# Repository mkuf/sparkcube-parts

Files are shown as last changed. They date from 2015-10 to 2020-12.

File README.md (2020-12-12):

# sparkcube-parts
Modifications for the Sparklabs Sparkcube. <br>
<br>
All Parts can be printed without support. <br>
In Places where support is needed, there are small membranes that need to be drilled out after printing. <br>
See the "support" Folder in every FreeCAD File.

## case
Main File for anything related to the outer shell of the Printer. <br> 
These files are not compatible with the original Sparkcube, as my Printer is larger in X and Z. <br>
<br>
It sports a Electronics-Compartment made from bent Sheetmetal, Cutouts for fitting a Udoo Quad/Dual Board and a Touchscreen LCD Display. <br>
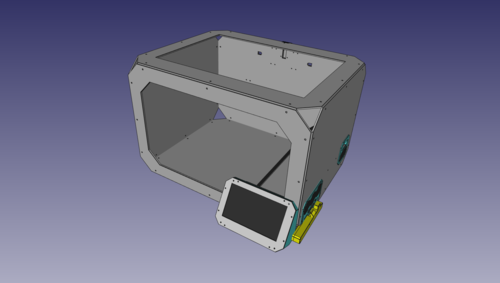
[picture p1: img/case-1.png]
case-1

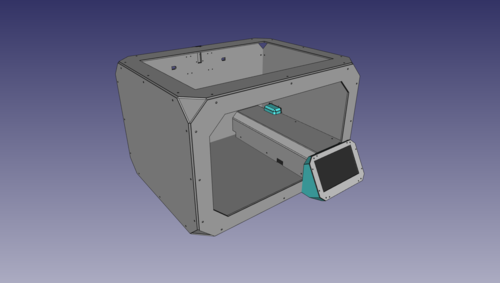
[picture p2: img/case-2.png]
case-2


## dual-mount
This is a X-Carriage and Mount for two E3Dv6 Hotends, as dropin for the stock Sparkcube carriage. <br>
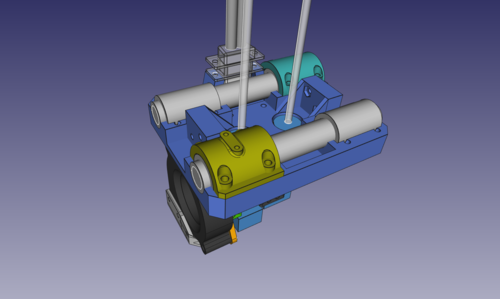
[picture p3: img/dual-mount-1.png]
dual-mount-1

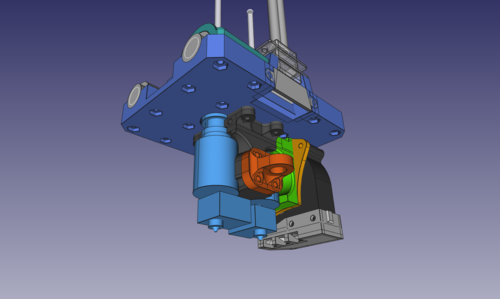
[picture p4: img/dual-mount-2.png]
dual-mount-2


## dual-x
With these Parts, a stock Sparkcube may be upgraded to use two independent Extruders for printing. <br>
Be aware that this reduces your Printarea in X by quite a bit. I recommend building your whole printer about 70mm wider. <br>
The design of these parts is inspired by the original Sparklab parts, but are not compatible with any of them (except the Z-Assembly of course). <br>
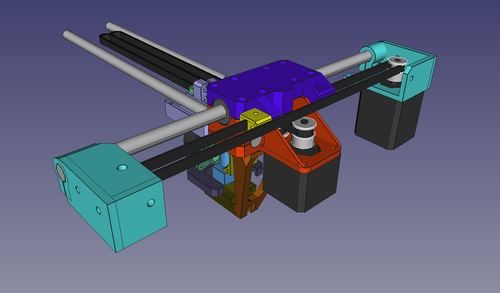
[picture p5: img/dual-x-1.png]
dual-x-1

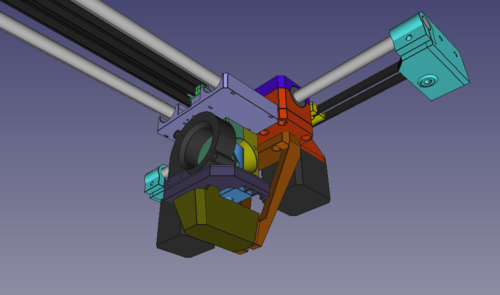
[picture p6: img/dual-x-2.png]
dual-x-2


## dual-x_z-assembly
Contains the `dual-x_bed_carrier`, that adjusts the placement of a standard MK2/3 Buildplate in Y to be compatible with the dual-x Setup <br>
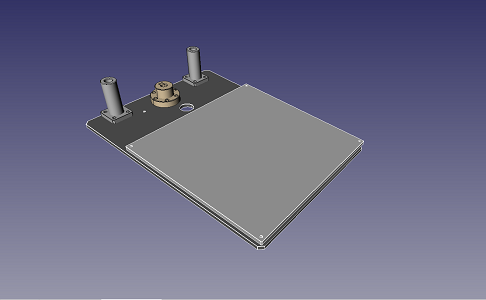
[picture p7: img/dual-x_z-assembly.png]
dual-x_z-assembly


## z-endstop-assembly
Minimalist solution to fine tune Z0. <br>
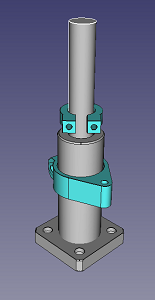
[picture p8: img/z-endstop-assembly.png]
z-endstop-assembly


## mpx-clip
A simple piece that clips around a MPX Connector to prevent it from accidential disconnecting. <br>
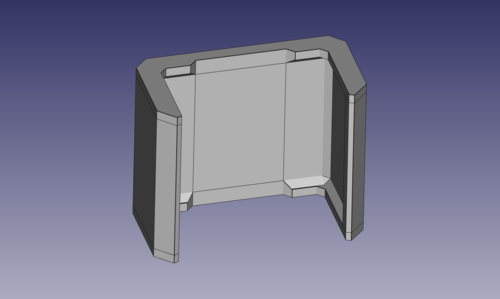
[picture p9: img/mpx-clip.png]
mpx-clip


## Spoolholder
A Spoolholder that is compatible with the Hole-Pattern found on the Back of the Case <br>
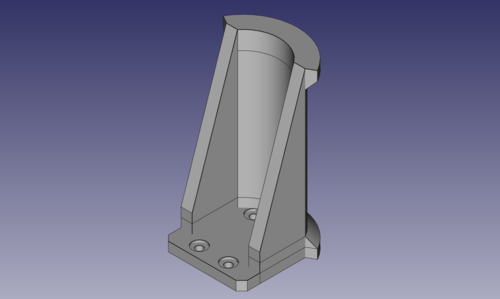
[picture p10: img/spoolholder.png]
spoolholder


## Webcam-Mount
A fixture to mount the PCB of a Logitech C270 Webcam to a Aluminium Extrusion without the need of any Screws. <br>
Just insert the Posts sideways into the Profile, rotate them 90°, screw in the baseplate and you're done. <br>
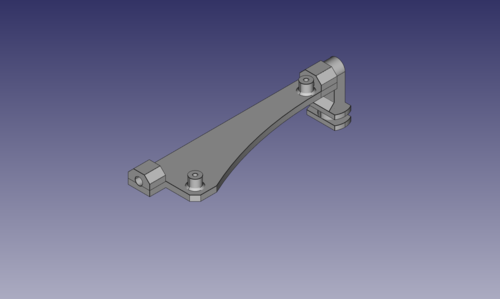
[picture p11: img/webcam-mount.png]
webcam-mount


Licensed under Creative Commons BY-NC-SA. <br>


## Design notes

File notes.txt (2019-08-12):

170,0W Heatbed
 40,0W H1
 40,0W H2
  1,2W F1
  1,2W F2
  1,2W HF1
  1,2W H-F2
  1,2W PSU-F
 35,0W Motors
  5,0W Udoo
  
~296W

+ LEDs
+ Touchscreen
+ Webcam

===================
Touchscreen Setup: 

apt-get install console-data
apt-get install xorg matchbox chromium-browser xserver-xorg-input-evdev unclutter haveged xdotool

===================

Stepper: 

X1/2: 0.72A
Y1/2: 0.8A
   Z: 0.6A
E1/2: 1.24A

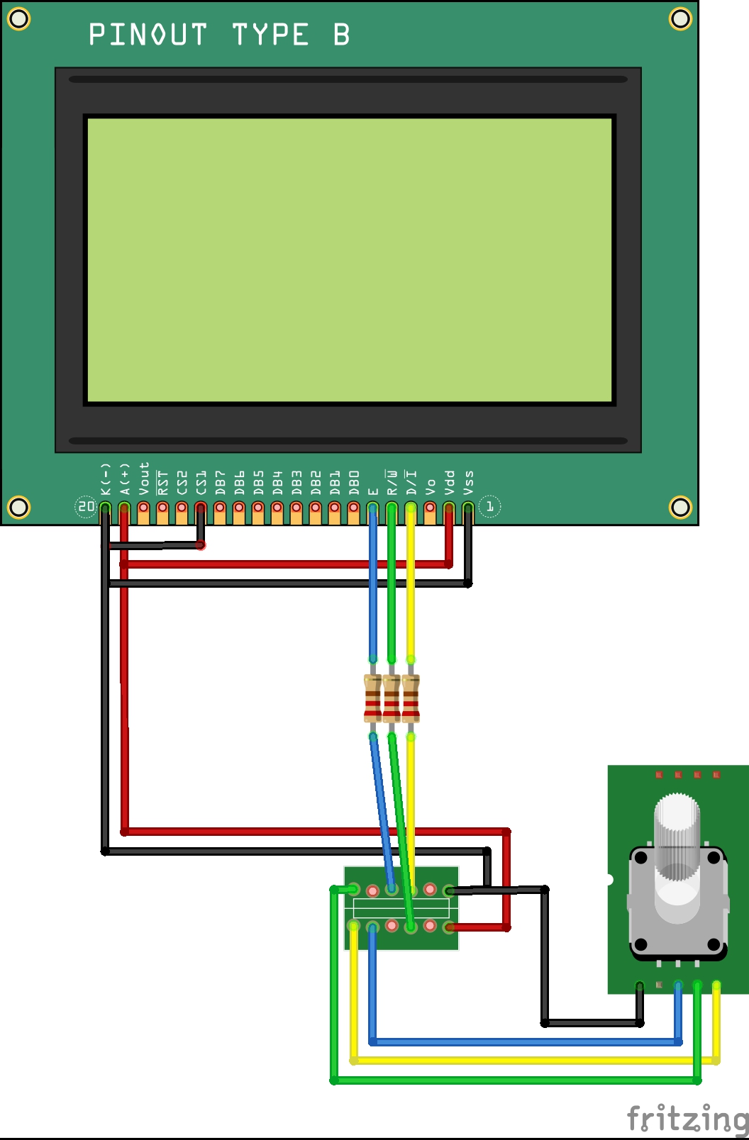
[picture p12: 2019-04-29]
img/RADDS_12864zw_Steckplatine.jpg

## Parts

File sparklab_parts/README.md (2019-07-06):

All Parts contained in this Folder are part of the official Sparklab Sparkcube Project.
http://the-sparklab.de/sparkcube-v1-1/

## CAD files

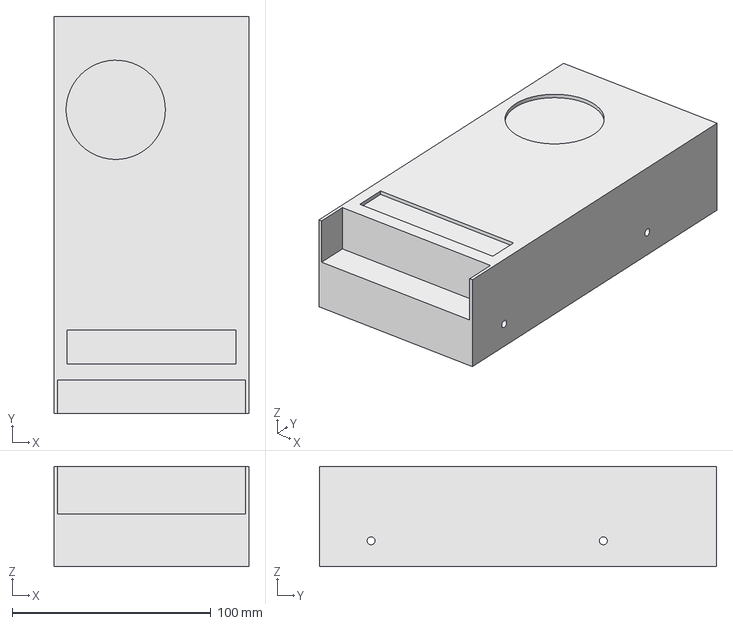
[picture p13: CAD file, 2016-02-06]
case/complete.fcstd
98.0 x 200.0 x 50.5 mm

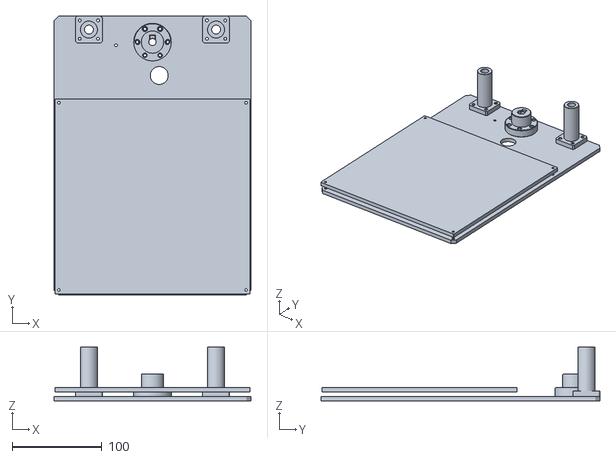
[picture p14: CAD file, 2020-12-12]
export/stl/z-assembly.stl
220.0 x 311.3 x 60.0

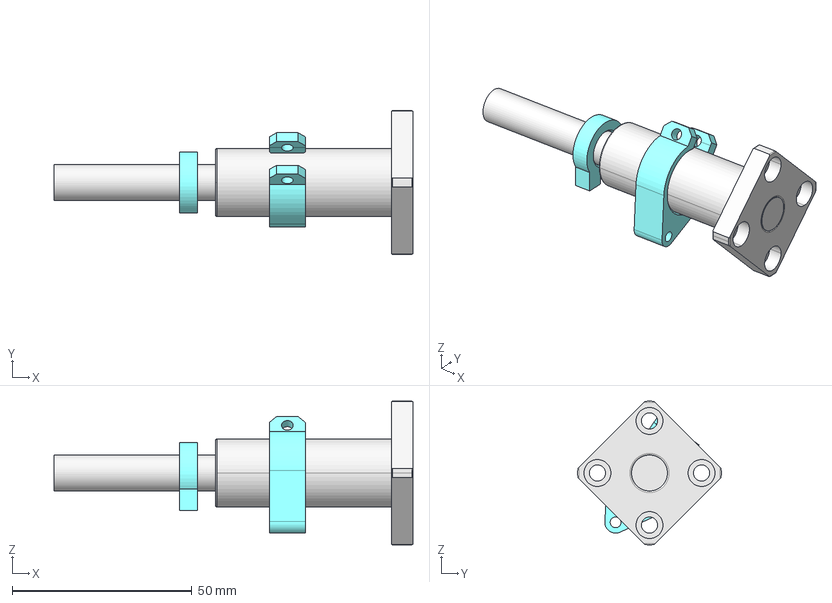
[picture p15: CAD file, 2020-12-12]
z-endstop-assembly.fcstd
100.0 x 40.0 x 40.0 mm
lmk10uu
10mm-smooth-rod
z-endstop-adjustment-ring
z-endstop-mount

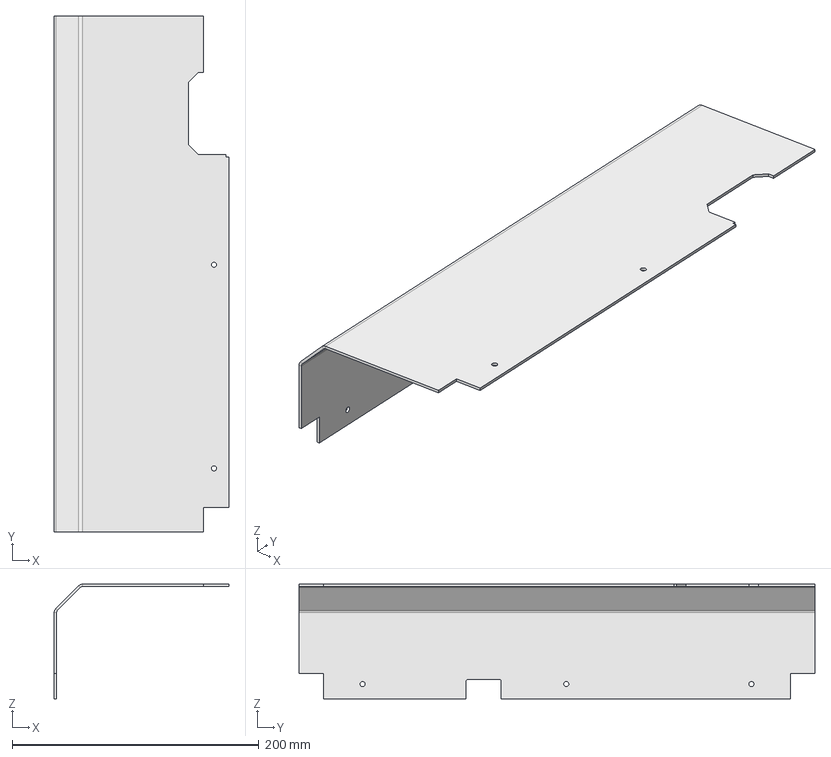
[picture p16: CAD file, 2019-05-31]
export/dxf/case/Electronics_Cover/Electronics_Cover_Solid.step
141.5 x 418.0 x 93.0 mm

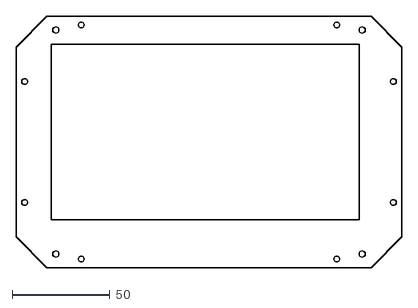
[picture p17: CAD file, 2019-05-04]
export/dxf/case/lcd_panel_2mm.dxf
197.8 x 128.8

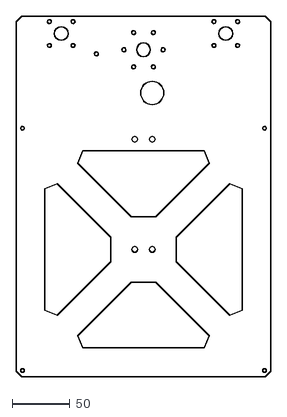
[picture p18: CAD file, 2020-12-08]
export/dxf/dual-x_bed_carrier.dxf
220.0 x 311.3

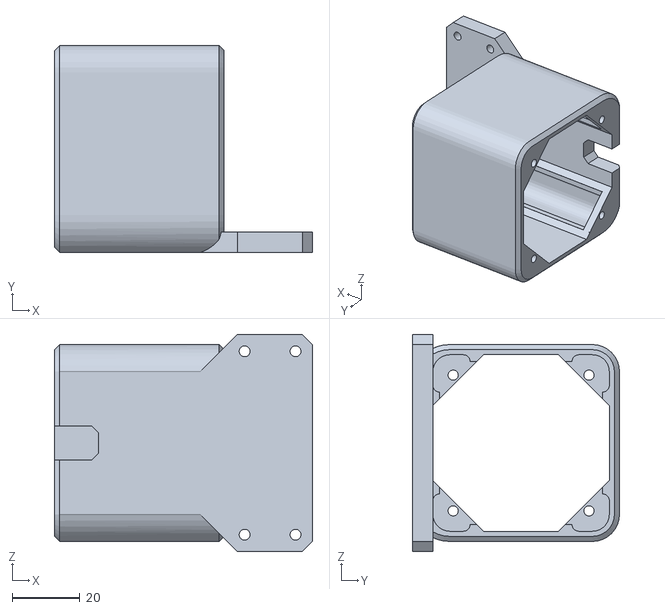
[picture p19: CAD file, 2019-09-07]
export/stl/case/extruder-decoupler.stl
76.0 x 61.0 x 64.0

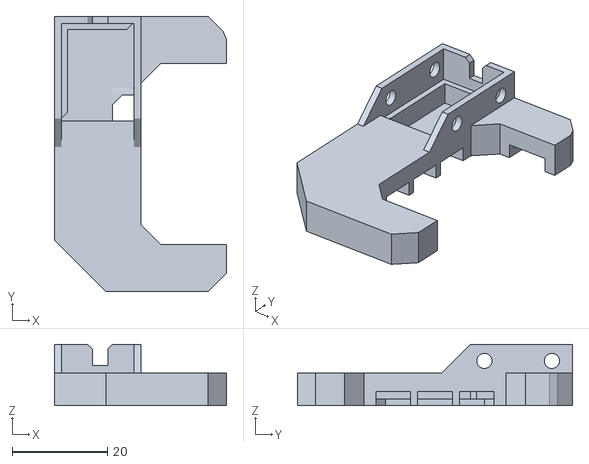
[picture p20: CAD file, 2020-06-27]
export/stl/dualx/fan-shroud_v2.stl
36.2 x 57.9 x 12.9

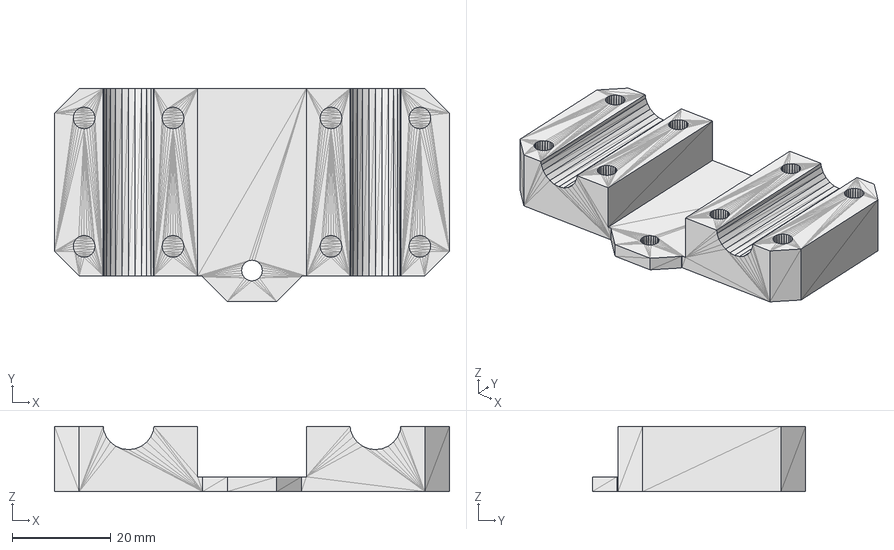
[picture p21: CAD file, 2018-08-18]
sparklab_parts/Converted/xend-c_2x.FCStd
80.0 x 43.2 x 13.2 mm

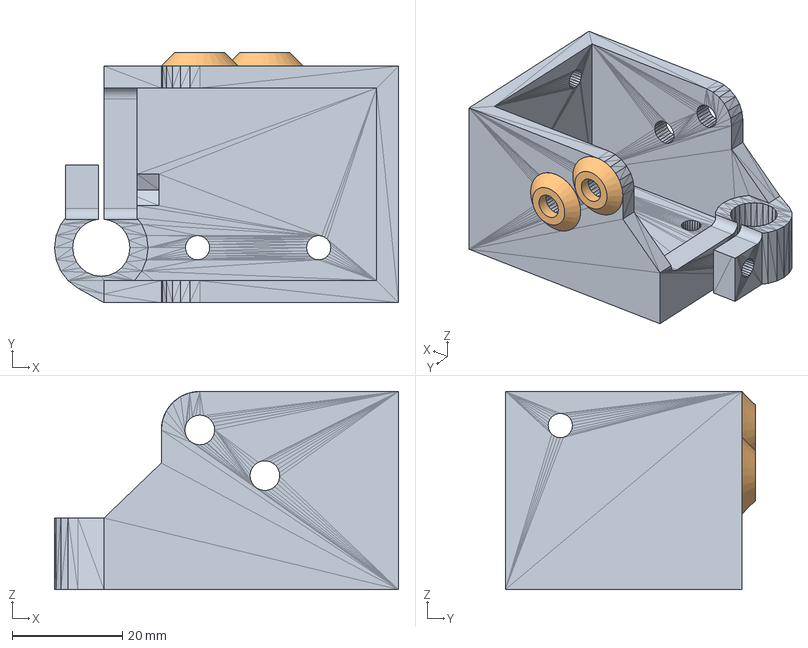
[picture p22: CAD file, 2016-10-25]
sparklab_parts/Mod/hendidler-r.fcstd
62.5 x 45.5 x 36.0 mm

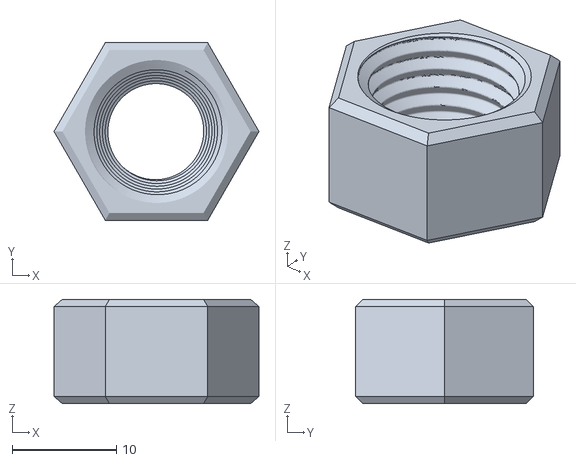
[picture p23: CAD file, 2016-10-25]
sparklab_parts/STL/coupling/[V2.5nut_5.stl
19.6 x 17.0 x 10.0

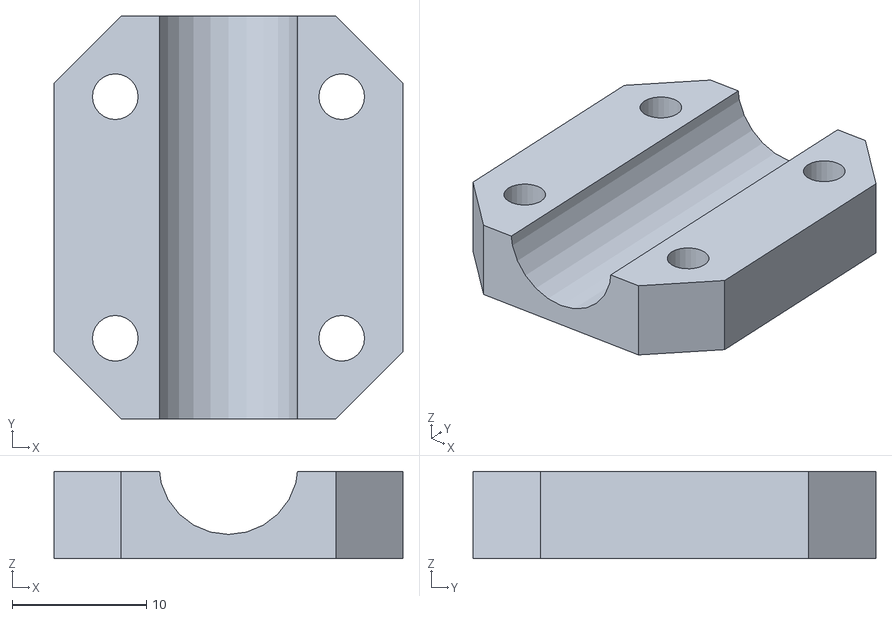
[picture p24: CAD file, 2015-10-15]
sparklab_parts/STL/zendstop-b.stl
26.0 x 30.0 x 6.50

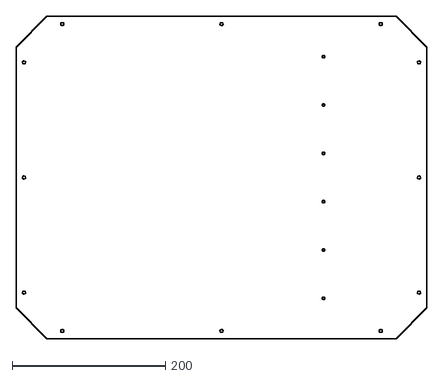
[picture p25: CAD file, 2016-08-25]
export/dxf/case/bottom_4mm.dxf
535.0 x 420.0

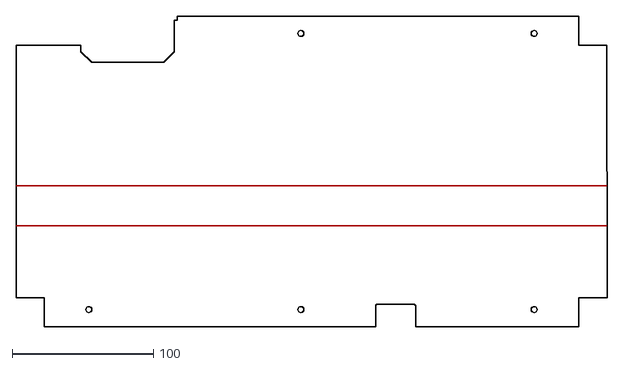
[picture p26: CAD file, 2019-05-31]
export/dxf/case/Electronics_Cover/Electronics_Cover_Unfold.dxf
418.0 x 219.3

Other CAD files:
dual-x_z-assembly.FCStd
export/stl/case/lrs-50-mount-p2.stl
export/stl/z-endstop-mount.stl
sparklab_parts/Converted/xend-a_2x.FCStd
case.FCStd
dual-x.FCStd
export/dxf/case/elec_side_2mm.dxf
export/dxf/case/elec_top_p1_2mm.dxf
export/dxf/case/elec_top_p2_2mm.dxf
export/dxf/case/front_4mm.dxf
export/dxf/case/inlet_cover_4mm.dxf
export/dxf/case/left_4mm.dxf
export/dxf/case/rear_4mm.dxf
export/dxf/case/right_4mm.dxf
export/dxf/case/top_4mm.dxf
export/stl/accessories_holder_0.2mm.stl
export/stl/case/bracket-mount.stl
export/stl/case/button-bracket.stl
export/stl/case/cable-inlet.stl
export/stl/case/electronics-cover-mount-bottom.stl
export/stl/case/electronics-cover-mount-side.stl
export/stl/case/exhaust_0.2mm_4peri.stl
export/stl/case/lcd_body_0.3mm.stl
export/stl/case/lcd_cable_armor.stl
export/stl/case/lcd_panel_spacer_0.2mm_6peri.stl
export/stl/case/lrs-50-mount-p1.stl
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

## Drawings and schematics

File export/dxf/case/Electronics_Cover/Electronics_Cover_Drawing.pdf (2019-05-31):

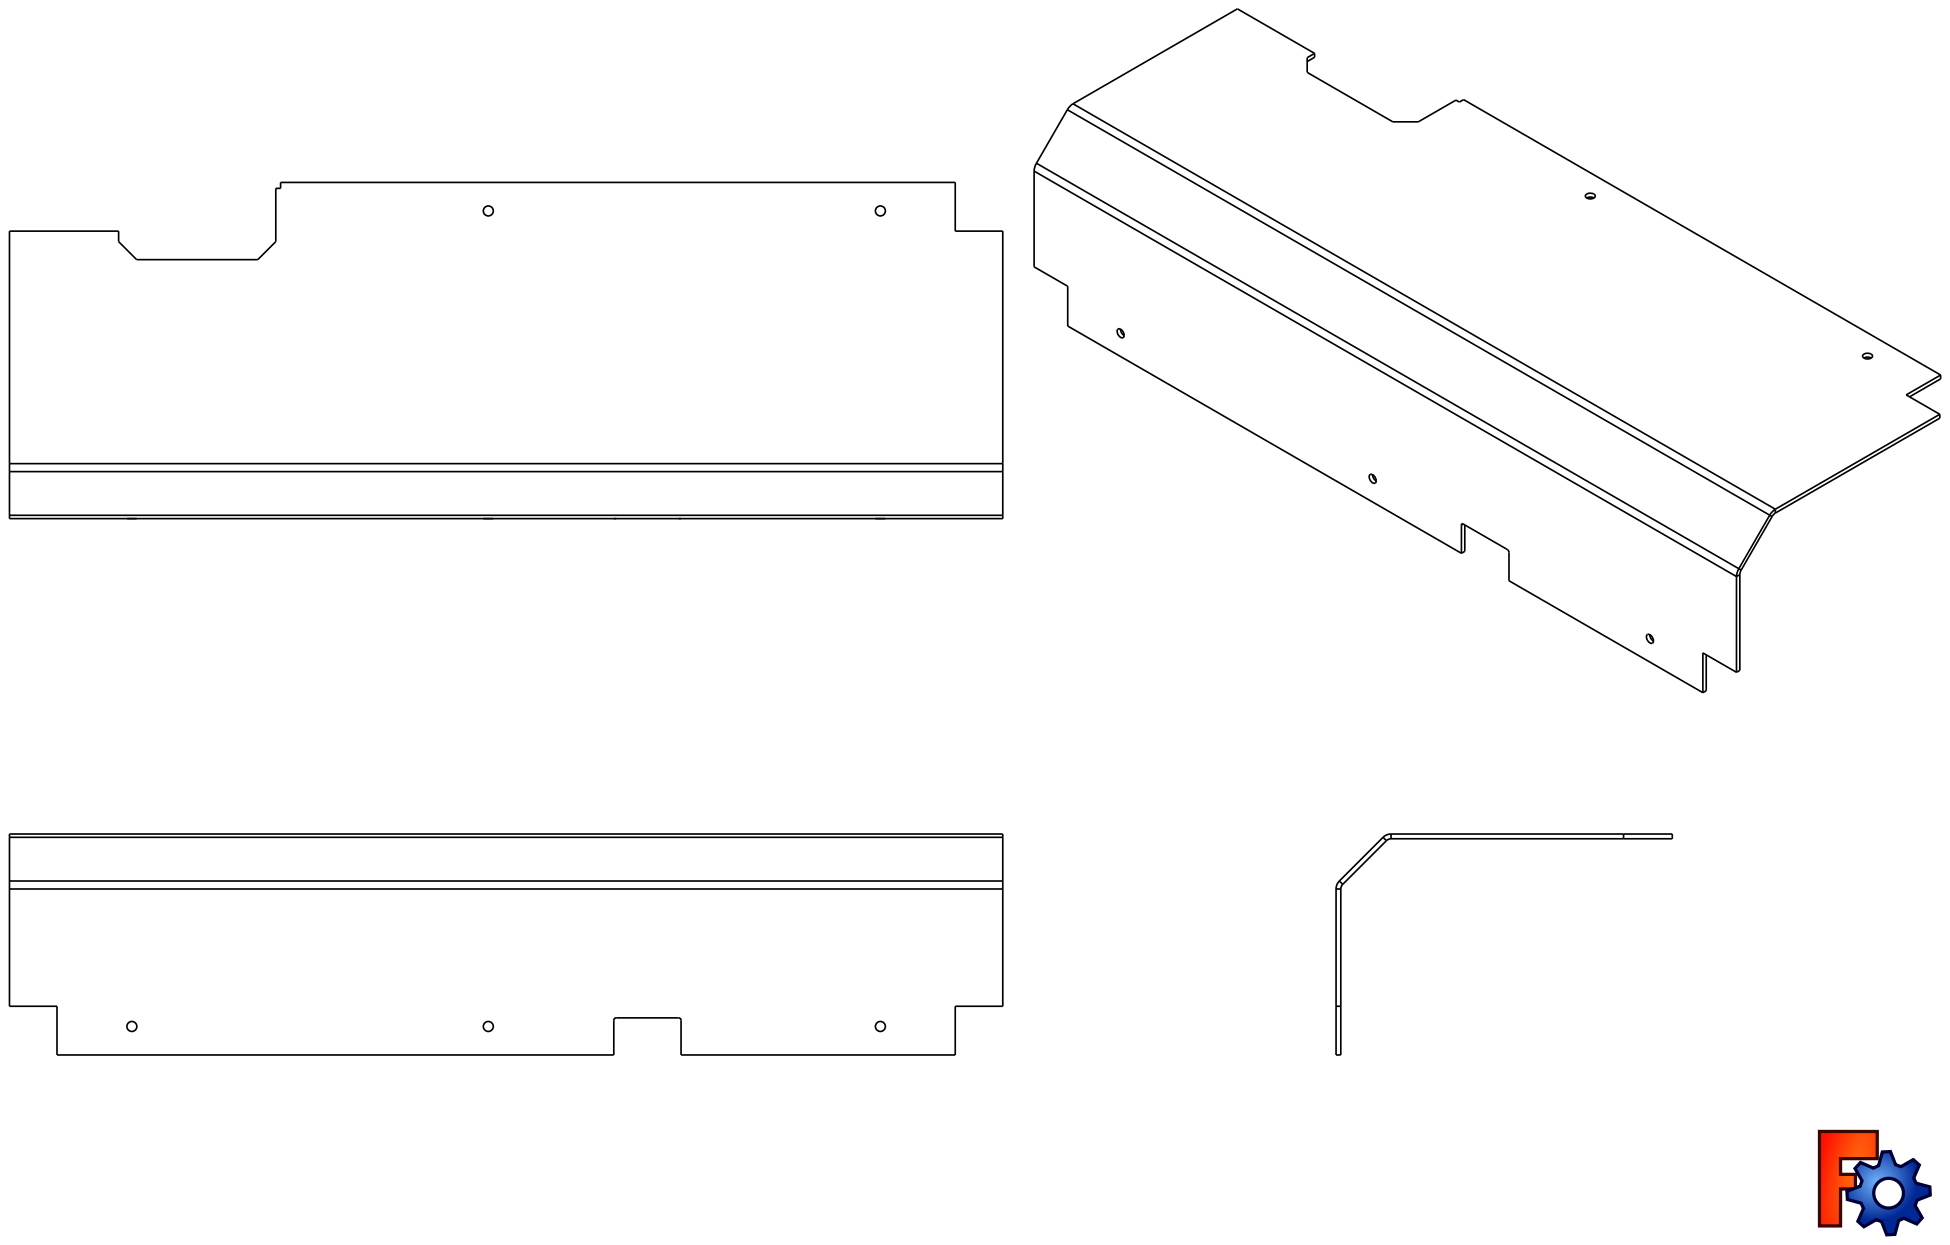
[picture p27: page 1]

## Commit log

2014-06-16 dual-mount halbiert mit 0.5mm versatz, schraubenloecher ausgeschnitten, erweiterungsbloecke angefuegt
    [dual-mount.FCStd]
2014-06-16 dual-mount angefast, zu _base umbenannt
    [dual-mount.FCStd, dual-mount_base.FCStd]
2014-06-17 Base ueberarbeitet, 23.0mm hotend abstand
    [dual-mount_base.FCStd]
2014-06-18 Dualmount: Befestigungsloecher und Grundflaeche hinzugefuegt
    [dual-mount_base.FCStd]
2014-06-19 Base: Verstaerkung an Befestigungsloechern hinzugefuegt
    [dual-mount_base.FCStd]
2014-06-19 Base: verstaerkungen f. schraubl. entfernt, material an basis entfernt
    [dual-mount_base.FCStd, dual-mount_muttern.fcstd, dual-mount_schraubenkoepfe.fcstd]
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2014-06-20 Base: Für hängende Befestigung angepasst, Versionen für Schraubenköpfe und Muttern gelöscht
    [dual-mount_base.FCStd, dual-mount_muttern.fcstd, dual-mount_schraubenkoepfe.fcstd]
2014-06-20 E3D: vervollständigt, Assembly: aktuellen stand testweise zusammengesetzt
    [E3Dv6.FCStd, dual-mount_base.FCStd]
2014-06-20 x-carriage: auf halterung angepasst, assembly: x-carriage hinzugefügt
    [assembly.fcstd, x-carriage.FCStd]
2014-06-20 Fanduct: Datei erstellt, z-probe: Modell zum größenvergleich
    [fanduct.fcstd, z-probe.fcstd]
2014-06-21 Fanduct: Base erstellt, E3D: für Fanduct angepasst
    [E3Dv6.FCStd, assembly.fcstd, fanduct.fcstd]
2014-06-27 fanduct_l: finalisiert, fanduct_r: neu erstellt
    [assembly.fcstd, fanduct_base.fcstd, fanduct_luefter.fcstd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]
2014-06-27 x-carriage: um 10mm auf 65mm innenmaß verlängert
    [x-carriage.FCStd]
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2014-09-20 Cabelguide v1, Airtripper Lock v2, Udoo-mount v0.1
    [guide.fcstd, lock.fcstd, mount.fcstd]
2015-01-11 Spindel inkl. Skizze hinzugefuegt
    [Spindel.fcstd]
2015-02-02 Laenge an neue Halterung angepasst
    [Spindel.fcstd]
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2016-01-24 udoo-mount entfernt, weiteres in 'case'
    [mount.fcstd]
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2016-05-05 Alle Teile nach Neuverkabelung
    [guide.fcstd]
2016-05-21 rand um udoo-panel verkleinert; löcher für psu_panelmount in bodenplatte verkleinert
    [front.fcstd]
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2016-06-27 ausgemistet; cableguide jetzt in cad_projects repo
    [guide.fcstd, halter.fcstd, halterV2.fcstd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]
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2016-08-25 fehler in Bottom-plate ausgebessert; alle Files in DXF und STL exportiert
    [bottom_4mm.dxf, bracket-mount.stl, button-bracket.stl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]
2016-10-25 Commit nach Finalem Zusammenbau; cable-inlet auf 3mm erweitert; smartctl-cover auf ist-werte revidiert; hendidler-l&r verstärkt und 2,5mm mehr Material um Schraubenlöcher
    [[V2.5_Kupplung_5_5.stl, [V2.5nut_5.stl, cable-inlet.stl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]
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2017-11-29 z-plate fixed
    [dual-x.FCStd]
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2018-08-18 rename dual-x to dual-x-linear_rails new dir dual-x-conversion
    [Motedis Profile 20x20 B-Type slot 6.stp, Motedis Profile 20x40 B-Type slot 6.stp, dual-x.FCStd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]
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2018-08-22 idler-bohrung zentriert; zylinder für idler-schraube angepasst; x-achse korrigiert
    [dualx_reconstructed.FCStd]
2018-08-25 unterer x-idler zu 90% fertig; mit oberen x-idler begonnen; idler an x-rod ausgerichtet
    [dualx_reconstructed.FCStd]
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2018-08-26 oberen x-idler um riemenspanner und gegenstück für umlenkrollen erweitert
    [dualx_reconstructed.FCStd]
2018-08-26 fasen an x-idler; farben; x-motor; lager kopiert; kegel für umlenkrolle in x-idler-A; idler und pulleys; pulley-spacer für xend und idler
    [dualx_reconstructed.FCStd]
2018-08-28 aufnahmen für rods in x-end-A um 0.15mm aufgeweitet
    [dualx_reconstructed.FCStd]
2018-08-29 Passungen für Linearwellen in idler, motormount und x-end-A vergrößert. Diese haben nun ein absolutes Übermaß von 0,2mm im Radius
    [dualx_reconstructed.FCStd]
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2018-08-31 x-carriage angepasst, damit kabelbinder zur lagerhalterung verwendet werden können
    [dualx_reconstructed.FCStd]
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2018-09-02 gespiegelte he-halterung entfernt und befestigungslöcher auf rückseite erweitert, damit kann die halterung universell montiert werden
    [dualx_reconstructed.FCStd]
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2018-09-11 Kabeldurchführung an Carriage vergrößert; Toleranzen an x-end-B für Lagerpressung angepasst
    [dualx_reconstructed.FCStd]
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2018-09-23 cable-inlet von 3 auf 6mm vergrößert f. dualx-verkabelung
    [cable-inlet.stl]
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2019-01-03 fix cable inlet for dual heads; add psu_fan_spacer; new windpipeV2
    [windpipe.stl]
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2019-01-06 fix fittings on bucket and bucket-holder; fix spoolholder diameter
    [bucket-holder.stl, dualx_reconstructed.FCStd, purge-bucket.stl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]
2019-04-28 create cleaned up version of case from current master (be009e5fbe23d18afd40c7e15eef2adc4fd9e371) and tag Sparkcube_v1.0_working_plates
    [cleaned_up.FCStd]
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2019-05-04 add lcd_body, lcd_cable_armor, lcd_panel wip: electronics-cover made of bent sheetmetal exported: lcd_panel
    [case.FCStd, lcd_panel_2mm.dxf]
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2019-05-09 improved rigidity for lcd_body; added chamfer to lcd_cable_armor, fixed bottom wall of lcd_cable_armor
    [case.FCStd, lcd_body_0.3mm.stl, lcd_cable_armor.stl]
2019-05-15 electronics_cover side-mount first draft; fix screwholes in lcd_body; add lcd_panel_spacer
    [accessories_holder.FCStd, accessories_holder_0.2mm.stl, case.FCStd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]
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2019-05-23 fix cable_armor
    [case.FCStd, lcd_cable_armor.stl]
2019-05-30 Major Rework for new PSU and Electronics Cover
    remove smartctl-cover
    remove psu
    remove psu-fan-spacer
    remove psu-fan
    remove elec_side_mount_start/middle/end
    remove elec_top_mount_start/p2/end
    rework exhaust
    rework power_panel
    rework electronics-cover
    add electronics-cover-mount-side
    add electronics-cover-mount-bottom
    add lrs-350
    add power_panel_cover
    [case.FCStd, elec_end.stl, elec_middle_2x.stl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]
2019-05-31 Reduce Chamfer in Electronics_Cover from 25 to 20mm; add flattened electronics_cover and a 2D-Drawing of it to export
    [Electronics_Cover_Solid.step, Electronics_Cover_Unfold.dxf, case.FCStd]
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2019-07-13 add psu mounting holes to bottom panel; add drilling template for psu mounting holes
    [case.FCStd, psu-mounting-template.step]
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2019-07-22 remove psu-mounting-template to fix compatibility with freecad 0.18
    [case.FCStd]
2019-07-23 add mountings for lrs-50 psu; add cover for heatbed mpx
    [case.FCStd]
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2020-02-14 dual-x: rework purge-bin
    [bucket-holder.stl, dual-x.FCStd, purge-bin-arm.stl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]
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2020-12-08 add new z-assembly to use with dual-x; add z-endstop-assembly.fcstd; remove z-endstop-adapter.fcstd;
    [dual-x_z-assembly.FCStd, dual-x_z-assembly.dxf, z-assembly.stl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]
2020-12-12 Add z-endstop-assembly Update dual-x_z-assembly to final dimensions Removed accesories_holder Update README
    Add Images of new Parts
    Export new Parts als STL/DXF
    [accessories_holder.FCStd, dual-x_bed_carrier.dxf, dual-x_z-assembly.FCStd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]

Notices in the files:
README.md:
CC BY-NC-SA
